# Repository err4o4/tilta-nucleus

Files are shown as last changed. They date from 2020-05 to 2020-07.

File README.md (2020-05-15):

# Tilta Nucleus N Protocol

First night tests and writeup. Please check all info with tester (multimeter) before connecting, I could be wrong

It uses standart UART 115200 to communicate to other Tilta devices. Both handunit and motor send exact same commands

## Pins on handunit

```
|-----------------|
| TX   +   +  GND |
|          +  ??? |
| RX?  +   +  GND |
|-----------------|
```

## Pins on focus motor

```
|-----------------------|
| ---|----|----|------\ |
| ---|----|----|------/ |
| GND  TX   RX   4.2v   |
|-----------------------|
```

## Commands

All commands are hex 15 chars long, starting with ":"

#### Sent every sec. Assume ping or heartbeat

```
:96060002000161
:C90680000000B1
```
#### Sent when focus changed by handunit. 

010601 - focus cmd

75 - ? 

270D - focus value 

4F - ? (checksum maybe)

```
:010601 75 270D 4F
```

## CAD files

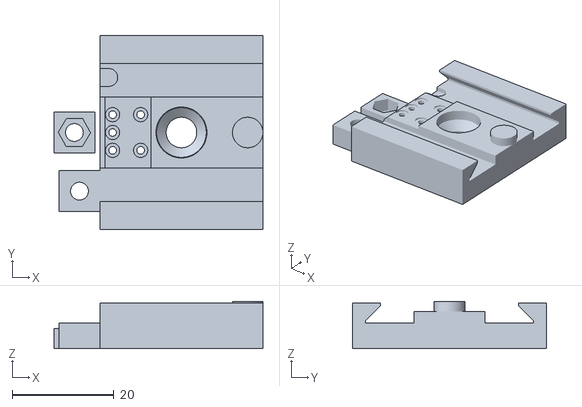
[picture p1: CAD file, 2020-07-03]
stl/Tilta Nucleus-N Assembly Clamp.stl
41.0 x 38.0 x 9.30

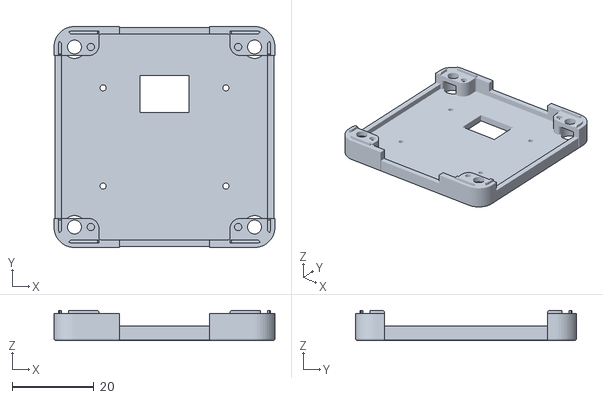
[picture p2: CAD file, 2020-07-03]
stl/Tilta Nucleus-N M5Stack.stl
54.0 x 54.0 x 7.40

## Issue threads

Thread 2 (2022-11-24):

Tilta Nucleus N MDR protocol specs

mcorrigan, 2022-11-24:
Hey I happen to have more specs for the TTL UART protocol for this device, but I'm currently trying to figure out how to tap into the unit (USB, internal pins? my strengths are software). Are you interested in collaborating on this or at least helping me get going?

mcorrigan, 2022-12-17:
SERIAL DATA FORMAT
1 - BIT RATE: 115200
2 - DATA LENGTH: 8 BIT
3 - STOP BIT: 1 BIT
4 - PARITY: NONE
5 - COMMUNICATION STANDARD: TTL UART serial Port-3.3V

COMMAND BLOCK DATA CONSTRUCTION
<start>(1 byte): 0x3A
MODEL ID (1 byte): 0x01
COMMAND (1 byte): 0x06
PARAM ID (2 bytes): 0x0001
DATA (2 bytes): 0x0001
Checksum (2 bytes): 0xF7
<CR> <LF> (2 bytes): 0x0D 0x0A

Refer to Modbus ASCII
COMMAND is always 0x06
CHECKSUM Example:
Checksum = 0x100- (MODEL ID + COMMAND + ParamID_H+ ParamID_L+ DATA _H+ DATA _L)
Checksum
     = 0x100- (0x01 +0x 06 + 0x 00+ 0x 01+ 0x 00+ 0x 01)
     =0x100-0x09
     =0xF7

:010600010001F7<CR> <LF>

caseybasichis, 2023-06-13:
Is the intention to control the Tilta with a wired connection?

mcorrigan, 2023-07-09:
>

Yep

caseybasichis, 2023-10-30:
Just picked up a Nano ii, going to attempt wired control this week.

Have you had a chance to test their latest?

philippjeschek, 2023-10-30:
You can contact Tilta directly to get the protocol specs for Tilta Nucleus Nano/M motors, but you have to sign a NDA to get it

caseybasichis, 2023-12-06:
Tempting, but uneasy signing an NDA with them.

I've been tinkering with GPT4 and the info from this repo, but it looks like the system doesn't register any change with `ls /dev/tty*` when plugging it in.

Is that expected?

This is the code soup GPT kicked out:
```
import time
import serial

# Calculate the 8-bit checksum using 2's complement
def calc_checksum(data):
    sum = 0

    # Sum all the bytes in the data
    for byte in data:
        sum += byte

    # Take the 2's complement of the sum
    return (~sum + 1) & 0xFF

def send_command(device_id, cmd, param, data):
    # Build the command
    command = bytearray([device_id, cmd, param >> 8, param & 0xFF, data >> 8, data & 0xFF])
    checksum = calc_checksum(command)
    msg = b":" + bytes(command) + bytes([checksum]) + b"\r\n"

    # Send the command
    ser.write(msg)

ser = serial.Serial(
    port='/dev/ttyS9',\
    baudrate=115200,\
    parity=serial.PARITY_NONE,\
    stopbits=serial.STOPBITS_ONE,\
    bytesize=serial.EIGHTBITS,\
    timeout=0)

print("Connected to: " + ser.portstr)

device_id = 1
cmd_focus = 5
param_speed = 0
data_min = 0
data_max = 9999

while True:
    try:
        # Send focus command with increasing data value
        for data in range(data_min, data_max):
            send_command(device_id, cmd_focus, param_speed, data)
            time.sleep(0.01)  # Adjust this sleep time as needed for the desired movement speed

        # Send focus command with decreasing data value
        for data in range(data_max, data_min, -1):
            send_command(device_id, cmd_focus, param_speed, data)
            time.sleep(0.01)  # Adjust this sleep time as needed for the desired movement speed

    except KeyboardInterrupt:
        print("Closing...")
        ser.close()
        break
```

Are any of you using this day to day?

maxholgasson, 2024-01-30:
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

Were you sucessful with this attempt? I'm able to open the connection, your python script is properly compiled but the motor doesn't do anything

caseybasichis, 2024-01-31:
Not yet.

My next step was to look at the code here -- three of the first generation motors running..
https://github.com/RainbowLabsDE/Fujinon2TiltaNucleus

Does that look usable?

maxholgasson, 2024-01-31:
I'll have a look but got it working after some hours

caseybasichis, 2024-01-31:
You got the Nano 2 working?
I’d love to know the process.
Mine test unit is gathering dust in the hopes that someone gets it going.

maxholgasson, 2024-01-31:
It's just the older version nano without 2.

mcorrigan, 2024-01-31:
> It's just the older version nano without 2.

Did you use the script you posted above? Would be great to have that available.

mcorrigan, 2024-01-31:
> No the script above posted didnt work for me

What did you end up doing to get it working?

mcorrigan, 2024-02-01:
@maxholgasson this community thing works best when we are learners and sharers :)

ThomasDmr, 2024-04-22:
Hi,
I know the thread is a bit old, but did anyone manage to get a working code ?
@mcorrigan did you manage to connect to the Nucleus ? Otherwise, I might help you with that.

Thanks to all for the shared information !

mcorrigan, 2024-04-25:
@ThomasDmr To my knowledge, no one has figured it out yet. tbh, this hasn't been able to be a high enough priority for me with everything else, so I haven't gone back to mess with any of it. If you do get things working though, I know many of us would love to get this figured out.

ThomasDmr, 2024-05-06:
Hi guys,
I was able to put my hands on a set of Tilta Nucleus M this weekend and managed to make my custom controller work !
Here are the main guidelines to how I did it :

Electrical specs :
- The Nucleus M communicate through a 7 pin cable and requites LEMO - 7 pin connectors (like [this one](https://www.mouser.fr/ProductDetail/LEMO/EXG.0B.307.HLN?qs=g4eXmMl0Iew1SN7gjSNmdQ%3D%3D))
- The pinout is described [here](https://wodielite.com/wiki/index.php/Tilta_Nucleus-M).
- WARNING : the +5.4VDC (pin 4) is generated by the motors themselve, so this is an OUTPUT and should not be connected to another power source (like 3.3V).
- I used standard 3.3V TTL UART to communicate and it works perfectly.

Code :
I worked with an ESP32 combined with an Arduino framework. My library is C++ and should work on with most C++ compilers, but you will have to remove the Serial.println() debug features that only work in the Arduino environment.

The protocol has been well described by @mcorrigan, but the data is sent as ASCII values and not bytes... so the hex value 0xab will be sent in two ascii bytes corresponding to the characters "a" and "b". This was a surprise but it is coherent with the ASCII Modbus Protocol.

Here is my library :

TiltaSerialProtocol.h
`
#pragma once

#include "Arduino.h"

// Define protocol specefic variables
#define RAW_MSG_LENGTH      17      // init + 2 model + 2 command + 4 param + 4 data + 2 checksum + CR + LF
#define TOTAL_MSG_BYTES     7       // 1 model, 1 command, 2 param, 2 data, 1 checksum
#define TITLA_INIT_CHAR     0x3A
#define TILTA_CR_CHAR       0x0D
#define TILTA_LF_CHAR       0x0A

// Define constant values for Iris, Focus and Zoom messages
#define TILTA_FOCUS_MODEL   1
#define TILTA_IRIS_MODEL    2
#define TILTA_ZOOM_MODEL    4
#define TILTA_COMMAND       6
#define TILTA_PARAM         1280

// Define the message structure of the input ASCII data
typedef union
{
    struct __attribute__((__packed__))
    {
        uint8_t     model;
        uint8_t     command;
        uint16_t    param;
        uint16_t    data;
        uint8_t     checksum;
    };
    uint8_t raw[TOTAL_MSG_BYTES];
} numerical_packet;

// Define the message structure of the numerical output data
typedef union
{
    struct __attribute__((__packed__))
    {
        char     model[2];
        char     command[2];
        char     param[4];
        char     data[4];
        char     checksum[2];
    };
    char raw[RAW_MSG_LENGTH - 3];
} ascii_packet;

// Class managing the Tilta UART protocol
class TiltaSerialProtocol
{
    public:
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
mcorrigan, 2024-05-11:
Hey that's awesome @ThomasDmr, thanks for sharing! The Nucleus N doesn't have the same LEMO connector as the M, unfortunately, I have the Nucleus N. Did you come across anything that might indicate how to tap into the N by chance? Again, I really appreciate you sharing, it looks incredible.

ThomasDmr, 2024-05-12:
@mcorrigan I hope the code will help you and others, as the thread already has helped me so far 👍
I have only worked on the Nucleus M for a specific project and don't know much about the Tilta products.
Is the Tilta N the same as the Tilta Nano ? I have checked the manual, and it looks like it is only wireless communication, am I correct ?

mcorrigan, 2024-05-14:
Yeah I think those are the same thing, and yeah it's wireless. With the name of the repo, I was hoping to find a way to tap into that, even at a hardware level (cracking it open and wiring directly into the PCB).

caseybasichis, 2024-05-17:
I ordered a Nucleus M — testing when I get back in town.

I also have a nano II and the mini mirage matte box motor.
Does this look promising?
https://www.facebook.com/groups/REDKomodoUsers/permalink/1241421903407551/?mibextid=W9rl1R

mcorrigan, 2024-05-18:
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

Hmm, I'm not sure. The Nucleus N is at work, but to memory it was a micro usb connection. But still, if I could get my hands on one of these cables, we could see if it is a passthrough patch cable or if there is additional circuitry in it. like a RS232->TTL or something.

ThomasDmr, 2024-05-21:
> Yeah I think those are the same thing, and yeah it's wireless. With the name of the repo, I was hoping to find a way to tap into that, even at a hardware level (cracking it open and wiring directly into the PCB).

Sorry for the late reply, I was on vacation.

I don't know anything about the wireless protocol for the nucleus, I only discovered their existence a few weeks ago for a project I'm doing for someone else.
If you want to control the Nucleus N you will sadly have to dig deeper into the wireless communication. Is it WiFi, Bluetooth or something else ?
Not sure I will be of great help to you with that, I'm sorry.

ThomasDmr, 2024-05-21:
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

I'm not an expert in Nucleus hardware, but this cable looks like it is mainly for power supply. I see only 3 connectors on one side which doesn't leave any place for data transmission (one would be GND, another VCC and the third I don't know).

mcorrigan, 2024-05-21:
Yeah I also noticed it has 3 pins on the connector, I assumed the last one is a half duplex data pin, but I don't know without throwing a scope on it.

wallydeedo, 2024-06-03:
The nucleus n has a small jack socket. I believe maybe standard 3.3V TTL UART .. The Tilta N, M wireless hardware uses Zigbee pro ‘Off-The-Shelf’ serial modules…

VID-PRO, 2025-08-28:
the 3.5mm jack on the nucleus N Motor is a TTL UART.
Pins on focus motor
```
|-----------------------|
| ---|----|----|------\ |
| ---|----|----|------/ |
| GND  TX   RX   4.2v   |
|-----------------------|
```

is there any complete example how to control the motor avaiable?

VID-PRO, 2025-09-21:
Thank you very much.
I sorted it out with this code:

```
for (int i = 0; i < 17; i++) {
      ZoomSerial.write(zoomCommand[i]);
}
```

one question is open.
How to i send the rec on (:C9060000000130) and rec off (:C9060000000131)  commands?

ThomasDmr, 2025-09-22:
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

I don't know these commands sorry, my code didn't require sending those.

But they should have the same format as the rest of the protocol.
I recommend that you first try to parse them to extract these variables but applied to your commands (many should be identical):
// Define protocol specefic variables
#define RAW_MSG_LENGTH      17      // init + 2 model + 2 command + 4 param + 4 data + 2 checksum + CR + LF
#define TOTAL_MSG_BYTES     7       // 1 model, 1 command, 2 param, 2 data, 1 checksum
#define TITLA_INIT_CHAR     0x3A
#define TILTA_CR_CHAR       0x0D
#define TILTA_LF_CHAR       0x0A

// Define constant values for Iris, Focus and Zoom messages
#define TILTA_FOCUS_MODEL   1
#define TILTA_IRIS_MODEL    2
#define TILTA_ZOOM_MODEL    4
#define TILTA_COMMAND       6
#define TILTA_PARAM         1280

Then you might have to add a function to my library (eg: encodeNewRecOn or encodeNewRecOff) and apply the same logic as for the FIZ commands.

Hope this helps, good luck !

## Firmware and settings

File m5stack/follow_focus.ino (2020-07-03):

#include <M5Stack.h>
#include "icons.h"  
#include "ArduinoJson.h"




#include <WiFi.h>
#include <WiFiUdp.h>
const char * networkName = "Home WiFi";
const char * networkPswd = "pixel2013";
const char * udpAddress = "192.168.88.220";
const int udpPort = 1234;
boolean connected = false;
WiFiUDP udp;



String readString, cmd, cmd_val;
int focus_val = 0;
int focus_val_prev = 0;
float focus_val_metric = 0;
float focus_val_metric_prev = 0; 

int cal_data_points_coint = 6;


struct LensData {
  char lens_name[32];
  float cal_data[128][2];
};

void setup() {
  M5.begin();
  M5.Lcd.fillScreen(TFT_BLACK);
  
  Serial.begin(115200);
  Serial2.begin(115200, SERIAL_8N1, 16, 17);


  // udp

  connectToWiFi(networkName, networkPswd);

  // udp 



  

  M5.Lcd.drawXBitmap(138, 88, logo, logoWidth, logoHeight, TFT_WHITE);
  delay(500);
  M5.Lcd.clear(BLACK);

  LensData LensData;
  load_lens_data(&LensData);
  print_header(&LensData, 0, 0, 0);
  print_buttons("set", "menu", "...");
  print_focus_ring(&LensData);
  print_rec_button(false);

}

void loop() {
  while (Serial2.available()) {
    if (Serial2.available() >0) {
      char c = Serial2.read();
      readString += c;
    }
  }

  if (readString.length() >0) {
      cmd = readString.substring(0, 6); 
      cmd_val = readString.substring(9, 13); 
      
      if(cmd == ":01060") { // focus cmd
        focus_val = strtol(cmd_val.c_str(), 0, 16)/10;
      }           
    readString="";
  }


  //udp

  


  // udp
  
    //here
    LensData LensData;
    update_focus_ring(&LensData);
    
    // make separate functions for header, rec, focus wheel, bottom button
}




void print_header(struct LensData* LensData, int wifi, int camera, int link) {
    M5.Lcd.drawString(LensData->lens_name,  2, 4, 2);
    M5.Lcd.drawXBitmap(241, 2, wi_fi_bits, wi_fi_width, wi_fi_height, TFT_WHITE);
    M5.Lcd.drawXBitmap(271, 2, camera_bits, camera_width, camera_height, TFT_WHITE);
    M5.Lcd.drawXBitmap(301, 4, link_bits, link_width, link_height, TFT_WHITE);
}

void print_buttons(String left, String center, String right){
    M5.Lcd.drawString(left,  55, 220, 2);
    M5.Lcd.drawString(center, 145, 220, 2);
    M5.Lcd.drawString(right,  250, 220, 2);
}

void print_rec_button(bool state){
  if(state) {
    M5.Lcd.drawXBitmap(128, 38, rec_bits, rec_width, rec_height, TFT_RED);
  } else {
    M5.Lcd.drawXBitmap(128, 38, rec_bits, rec_width, rec_height, TFT_WHITE);
  }
}

void print_focus_ring(struct LensData* LensData) {
  M5.Lcd.setTextDatum(MC_DATUM);
  
  M5.Lcd.drawString("          ", 150, 130, 6);
  M5.Lcd.drawString(String(focus_val), 160, 130, 6);
  
  M5.Lcd.setTextDatum(TL_DATUM);
  M5.Lcd.drawFastHLine(70, 180, 180, TFT_WHITE); // focus line
  //M5.Lcd.drawFastVLine(map(focus_val, 0, 999, 70, 250), 175, 10, TFT_WHITE); // focus current

  for (int i=0; i <= cal_data_points_coint; i++){
    Serial.println(LensData->cal_data[i][0]);
    Serial.println(LensData->cal_data[i][1]);
    
    String point_name = String(LensData->cal_data[i][0]);
    
    if(int(LensData->cal_data[i][0]) == 999) {
      point_name = "inf";
    } 
    
    //M5.Lcd.drawFastHLine(70, 180, 180, TFT_WHITE); // focus line
    if ( (i % 2) != 0) {
      M5.Lcd.drawString(point_name, map(int(LensData->cal_data[i][1]), 0, 999, 70, 250) - 10, 195, 2); 
      M5.Lcd.drawFastVLine(         map(int(LensData->cal_data[i][1]), 0, 999, 70, 250),      185, 5, TFT_WHITE); 
    } else {
      M5.Lcd.drawString(point_name, map(int(LensData->cal_data[i][1]), 0, 999, 70, 250) - 10, 155, 2); 
      M5.Lcd.drawFastVLine(         map(int(LensData->cal_data[i][1]), 0, 999, 70, 250),      170, 5, TFT_WHITE); 
    }
    
  }

}

void update_focus_ring(struct LensData* LensData) {
      int target = focus_val;
      byte nearindex = 0;
      int neardiff = abs(int(LensData->cal_data[0][1]) - target);
      
      for (byte i = 1; i < cal_data_points_coint; i++) {
        if (abs(int(LensData->cal_data[i][1]) - target) < neardiff) {
          nearindex = i;
          neardiff = abs(int(LensData->cal_data[i][1]) - target);
        }
      }

      if(target > LensData->cal_data[nearindex][1]) {
       focus_val_metric = mapf(target, LensData->cal_data[nearindex][1], LensData->cal_data[nearindex+1][1], LensData->cal_data[nearindex][0], LensData->cal_data[nearindex+1][0]);
      } else {
       focus_val_metric = mapf(target, LensData->cal_data[nearindex-1][1], LensData->cal_data[nearindex][1], LensData->cal_data[nearindex-1][0], LensData->cal_data[nearindex][0]);
      }

      if(abs(focus_val_metric - focus_val_metric_prev) > 0.01) {
        M5.Lcd.setTextDatum(MC_DATUM);
        M5.Lcd.drawString("              ", 150, 130, 6);
        if(LensData->cal_data[cal_data_points_coint-1][0] < focus_val_metric) {
          M5.Lcd.drawString(String("inf"), 160, 130, 4);
        } else {
          M5.Lcd.drawString(String(focus_val_metric), 160, 130, 6);
        }
        focus_val_metric_prev = focus_val_metric;


        // udp
        char senddata[20];
        String focus_val_metric_to_send = String(focus_val_metric);
        focus_val_metric_to_send += "\n";
        focus_val_metric_to_send.toCharArray(senddata, sizeof(senddata));
        if(connected){
          //Send a packet
          udp.beginPacket(udpAddress,udpPort);
          udp.printf(senddata);
          udp.endPacket();
        }
        // udp
        
        
      }

      if(focus_val_prev != focus_val) {
        M5.Lcd.setTextDatum(TL_DATUM);
        M5.Lcd.drawFastVLine(70, 175, 10, TFT_WHITE); // focus mark min
        M5.Lcd.drawFastVLine(250, 175, 10, TFT_WHITE); // focus mark max
        
        M5.Lcd.drawFastVLine(map(focus_val_prev, 0, 999, 70, 250), 175, 10, TFT_BLACK); // clear prev focus mark
        M5.Lcd.drawFastHLine(70, 180, 180, TFT_WHITE); // focus line
        M5.Lcd.drawFastVLine(map(focus_val, 0, 999, 70, 250), 175, 10, TFT_WHITE); // focus current
        focus_val_prev = focus_val;
      }


      
}

bool load_lens_data(struct LensData* LensData) {
    StaticJsonDocument<900> doc;
    char json[] =   "{ \"cal_data\": [ [0.45, 0], [0.5, 145], [0.7, 429], [1, 629], [1.5, 761], [3, 874], [999, 999] ], \"lens\": \"Nikon AF Nikkor 50mm f\/1.8D\" }";
    DeserializationError error = deserializeJson(doc, json);
    if (error) {
      Serial.print(F("deserializeJson() failed: "));
      Serial.println(error.c_str());
    }
    strcpy(LensData->lens_name, doc["lens"]);
    copyArray(doc["cal_data"], LensData->cal_data);
    return true;
}


double mapf(double val, double in_min, double in_max, double out_min, double out_max) {
    return (val - in_min) * (out_max - out_min) / (in_max - in_min) + out_min;
}



void connectToWiFi(const char * ssid, const char * pwd){
  Serial.println("Connecting to WiFi network: " + String(ssid));

  // delete old config
  WiFi.disconnect(true);
  //register event handler
  WiFi.onEvent(WiFiEvent);
  
  //Initiate connection
  WiFi.begin(ssid, pwd);

  Serial.println("Waiting for WIFI connection...");
}

//wifi event handler
void WiFiEvent(WiFiEvent_t event){
    switch(event) {
      case SYSTEM_EVENT_STA_GOT_IP:
          //When connected set 
          Serial.print("WiFi connected! IP address: ");
          Serial.println(WiFi.localIP());  
          //initializes the UDP state
          //This initializes the transfer buffer
          udp.begin(WiFi.localIP(),udpPort);
          connected = true;
          break;
      case SYSTEM_EVENT_STA_DISCONNECTED:
          Serial.println("WiFi lost connection");
          connected = false;
          break;
      default: break;
    }
}

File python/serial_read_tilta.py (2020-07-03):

import serial

ser = serial.Serial(
    port='/dev/tty.usbmodem1461401',\
    baudrate=115200,\
    parity=serial.PARITY_NONE,\
    stopbits=serial.STOPBITS_ONE,\
    bytesize=serial.EIGHTBITS,\
        timeout=0)

print("connected to: " + ser.portstr)

line = []

while True:
    for c in ser.read():
        line.append(c)
        if c == '\n':
            if((len(line) > 12)):
                if(''.join(line).replace('\r\n', '') != ':96060002000161' and ''.join(line).replace('\r\n', '') != ':C90680000000B1'):
                    focus = '0x' + line[9] + line[10] + line[11] + line[12]
                    an_integer = int(focus, 16)
                    print('focus', an_integer / 10)
            line = []
            break

ser.close()
